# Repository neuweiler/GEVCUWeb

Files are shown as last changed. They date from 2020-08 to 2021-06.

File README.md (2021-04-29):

GEVCU - Web
=================
by Michael Neuweiler

A replacement for the buggy GEVCU iChip. Use an ESP32 to connect via the existing serial interface
of the GEVCU. It provides the GEVCU web-site and data via websocket to a web browser.

## Advantages
* The operation is much more stable
* The communication is much faster because it's binary between GEVCU and ESP32. Thus the json data
for the web-browser is generated by the ESP32, not GEVCU - off-loading GEVCU from time consuming work and reducing strings of 10-20 bytes to 2-3 bytes
* With SPIFFS' 1.5MB there's three times more space for web-content than on iChip. With an SD card we're talking GB's and the possibility to store and present statistical data.

The configuration of the ESP32 is stored in data/config.json. Adjust it to your own needs. 

Connect with a laptop, mobile phone, tablet or Raspberry Pi to the WiFi network of the ESP32 ("GEVCU" by default) and in a web-browser open http://gevcu.local 

## Required libraries
* ArduinoJson
* ArduinoOTA
* https://github.com/me-no-dev/AsyncTCP
* https://github.com/me-no-dev/ESPAsyncWebServer
* ESPmDNS
* FS
* SD_MMC
* SPIFFS
* Update
* WiFi
* HTTPClient
* WifiClientSecure

## Required hardware
* ESP32 board with GPIO 12-17 exposed - if possible with SD card reader integrated (then only 16,17 are required) - a good choice is https://www.aliexpress.com/item/4000133143167.html - although an SC card is not mandatory for operation, future extensions like storing statistical data
will require it.
* SD card with FAT file system to store the web site data on (you may also use 1.5MB SPIFFS instead).
Upload the contents of the directory "data" to the root of the file system.
* GEVCU (General Electric Vehicle Control Unit) to connect to via Serial2 interface.

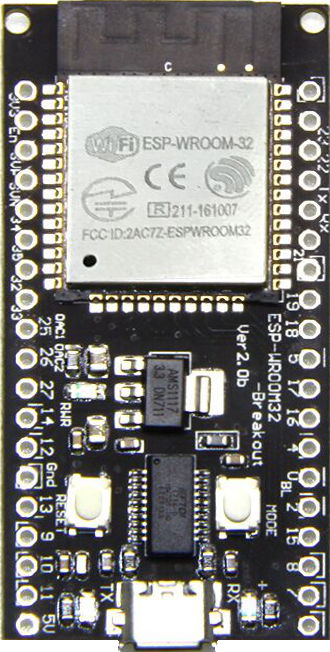
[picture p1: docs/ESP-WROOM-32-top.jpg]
BoardTop
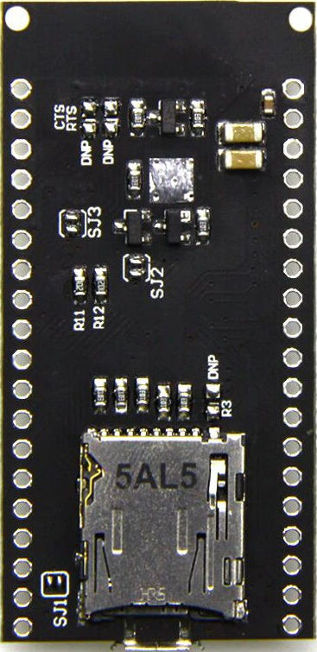
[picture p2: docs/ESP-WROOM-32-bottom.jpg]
BoardBottom
 

Note: To ensure flawless operation, increase the "max_files" config in SD_MMC.cpp from 5 to 20 !
      (in SDMMCFS::begin() , around line 72)

## Upload Parameters
* Board: ESP32 Dev Module
* Upload Speed: 921600
* CPU Freq: 240MHz
* Flash Freq: 80MHz
* Flash Mode: QIO
* Flash Size: 4MB (32Mb)
* Partition Scheme: Default with SPIFFS (1.2MB App, 1.5MB SPIFFS)
* Core Debug Level: none
* PSRAM: disabled
* Port: gevcu at 192.168.3.1 (for over the air update once a working copy has been installed via USB)

## Connect to GEVCU

The ESP32 must be connected the following way to GEVCU's wifi/iChip socket:
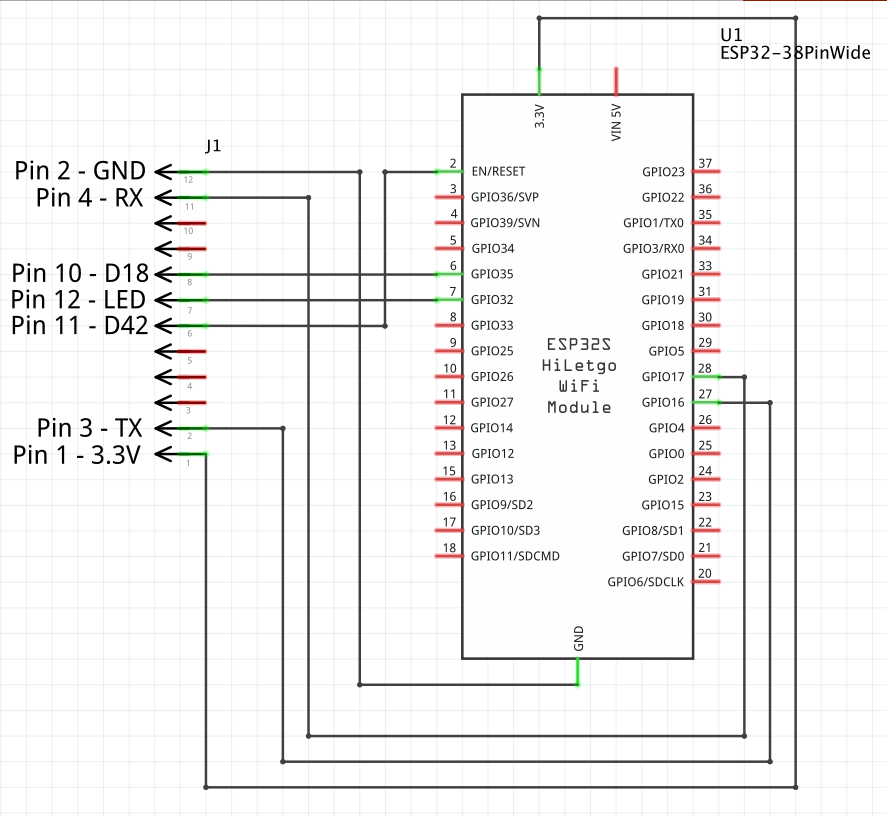
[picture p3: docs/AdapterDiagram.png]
Schema


With a simple adapter you can plug the ESP32 board right into the original socket. When creating the adapter board, make sure everything will fit in the GEVCU casing. And while you're at it, modify the board and attach an external antenna (like described here [External Antenna](https://www.hackster.io/simon-vavpotic/esp32-and-esp8266-external-antenna-f28e6b))
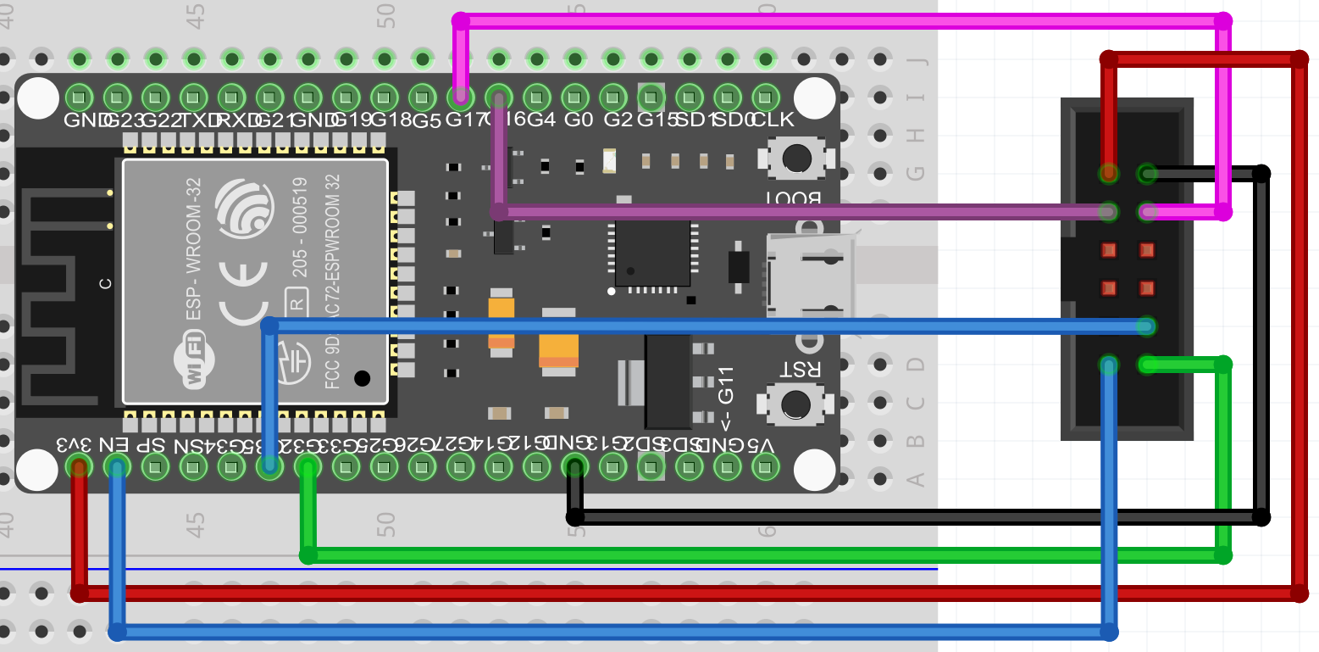
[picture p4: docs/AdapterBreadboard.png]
Adapter


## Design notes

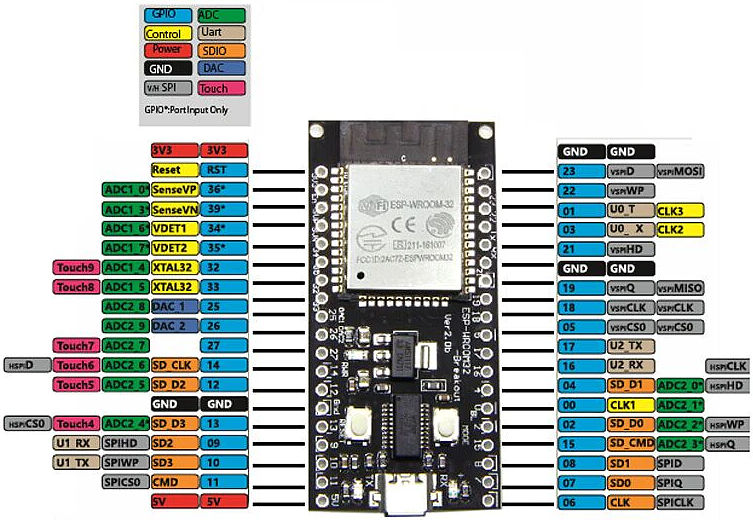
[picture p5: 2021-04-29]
docs/ESP-WROOM-32-pins.jpg

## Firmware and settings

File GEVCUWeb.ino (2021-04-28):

/*
 * GEVCU-ESP32Web.ino
 *
 Copyright (c) 2020 Michael Neuweiler

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
 */

#include "GEVCUWeb.h"

void setup() {
	logger.info("setup");

	config.load();

	wlan.init();
	webServer.init();
	webSocket.init(webServer.getWebServer());

	gevcuAdapter.init();

	heartBeat.init();
}

void loop() {
	delay(100);

	wlan.loop();
	gevcuAdapter.loop();
	webSocket.loop();
	heartBeat.loop();
}

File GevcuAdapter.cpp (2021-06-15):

/*
 * GevcuAdapter.cpp
 *
 Copyright (c) 2020 Michael Neuweiler

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
 */

#include "GevcuAdapter.h"

GevcuAdapter gevcuAdapter;

GevcuAdapter::GevcuAdapter() {
	bufPos = 0;
	binaryDataCount = 0;
	connectedClients = 0;
	timestamp = millis();
}

GevcuAdapter::~GevcuAdapter() {
}

void GevcuAdapter::init() {
	webSocket.subscribe(this);

	Serial2.begin(115200);
	Serial2.setRxBufferSize(4096);

	pinMode(PIN_GEVCU_LED, OUTPUT);
//    pinMode(PIN_GEVCU_RESERVED, OUTPUT);

	logger.info("GevcuAdapter configured");
}

String GevcuAdapter::getConfigParameter(String key) {
	return gevcuConfig[key];
}

void GevcuAdapter::setConfigParameter(String key, String value) {
	if (key && value && !value.equals(gevcuConfig[key])) {
		gevcuConfig[key] = value;
		Serial2.printf("cfg:%s=%s\r\n", key.c_str(), value.c_str());
		delay(50); // don't overwhelm GEVCU
	}
}

String GevcuAdapter::getLog() {
	Serial2.println("cmd:getLog");
	String log;
	uint32_t start = millis();
	while (Serial2.available() || (log.indexOf("LOG END") == -1 && (start + 3000) > millis())) {
		int ch = Serial2.read();
		if (ch != -1) {
			log.concat((char) ch);
		}
	}
	return log;
}

void GevcuAdapter::loop() {
	while (Serial2.available()) {
		int ch = Serial2.read();
//Serial.printf("%c (%X)\n", ch, ch);
		if (binaryDataCount > 0) { // expecting binary data
			serialBuffer[bufPos++] = ch;
			if (serialBuffer[0] == 0xaa) {
				if (bufPos > 2 && processBinaryData(serialBuffer[1], bufPos - 2, &serialBuffer[2])) {
					bufPos = 0;
					if (--binaryDataCount == 0) {
						String data;
						serializeJson(doc, data);
						if (logger.isDebug()) {
							logger.info("sending to websocket: %s", data.c_str());
						}
						webSocket.send(data);
					}
				}
			} else { // expecting binary data but got no valid lead char (0xaa) -> drop this entry
				logger.warn("dropping invalid data frame");
				bufPos = 0;
				binaryDataCount--;
			}
		} else if (ch == 13 || ch == 10 || ch == 0 || bufPos > SERIAL_BUFFER_SIZE - 1) { // process config/log data
			serialBuffer[bufPos] = 0;
			if (bufPos > 4) { // drop strings smaller than 4 characters
				processInput(serialBuffer);
			}
			bufPos = 0;
		} else if (ch != -1) {
			serialBuffer[bufPos++] = ch;
		}
	}

	if (timestamp + 10000 < millis()) {
		// if config is not loaded, request from GEVCU
		if (gevcuConfig["logLevel"] == NULL) {
			logger.warn("GEVCU config not loaded, requesting");
			Serial2.println("cmd:loadConfig");
		}
		String timeRunning = "{\"timeRunning\": \"" + getTimeRunning() + "\"}";
		webSocket.send(timeRunning);

		timestamp = millis();
	}
}

bool GevcuAdapter::processBinaryData(char code, uint16_t len, char *data) {
	DataPoint *dp = findDataPoint(code);
	if (dp && len < dp->length) {
		return false;
	}

	if (dp->length == 1 && dp->unsignd) {
		doc[dp->label] = (uint8_t) data[0];
	} else if (dp->length == 2 && dp->unsignd) {
		doc[dp->label] = (dp->divisor == 0 ? readUInt16(data) : readUInt16(data) / (double) dp->divisor);
	} else if (dp->length == 2 && !dp->unsignd) {
		doc[dp->label] = (dp->divisor == 0 ? readInt16(data) : readInt16(data) / (double) dp->divisor);
	} else if (dp->length == 4 && dp->unsignd) {
		doc[dp->label] = serialized(
				(dp->divisor == 0 ? String(readUInt32(data)) : String(readUInt32(data) / (double) dp->divisor)));
	} else {
		logger.warn("unable to process data: code %d, length %d", code, len);
	}
	return true;
}

uint32_t GevcuAdapter::readUInt32(char *data) {
	return (uint32_t) ((data[0] << 24) | (data[1] << 16) | (data[2] << 8) | data[3]);
}

int16_t GevcuAdapter::readInt16(char *data) {
	return (int16_t) ((data[0] << 8) | data[1]);
}

uint16_t GevcuAdapter::readUInt16(char *data) {
	return (uint16_t) ((data[0] << 8) | data[1]);
}

void GevcuAdapter::processInput(String input) {
	if (logger.isDebug()) {
		logger.debug("input from GEVCU: %s", input.c_str());
	}

	String data = extractData(input, "data:");
	if (data.length()) {
		binaryDataCount = data.toInt();
		doc.clear();
		return;
	}

	data = extractData(input, "cfg:");
	if (data.length()) {
		int pos = data.indexOf('=');
		if (pos > 0) {
			String key = data.substring(0, pos);
			String value = data.substring(pos + 1);
			gevcuConfig[key] = value;
		}
		return;
	}

	data = extractData(input, "json:");
	if (data.length()) {
		webSocket.send(data);
		return;
	}
	logger.warn("unknown data from GEVCU: %s", input.c_str());
}

String GevcuAdapter::extractData(String input, String identifier) {
	int index = input.indexOf(identifier);
	if (index == -1)
		return "";
	return input.substring(index + identifier.length());
}

void GevcuAdapter::event(String message) {
	if (message.equals("disconnected")) {
		if (--connectedClients == 0) {
			digitalWrite(PIN_GEVCU_LED, LOW);
			Serial2.printf("cmd:%s\r\n", message.c_str());
		}
	} else {
		if (message.equals("connected")) {
			connectedClients++;
			digitalWrite(PIN_GEVCU_LED, HIGH);
		}
		Serial2.printf("cmd:%s\r\n", message.c_str());
	}
}

void GevcuAdapter::sendHeartBeat(uint16_t count) {
	Serial2.printf("hb:%d\r\n", count);
}

void GevcuAdapter::stopHeartBeat() {
	Serial2.println("hb:stop");
}

void GevcuAdapter::startHeartBeat() {
	Serial2.println("hb:start");
}

DataPoint* GevcuAdapter::findDataPoint(char code) {
	for (int i = 0; i < sizeof(dataPoints); i++) {
		if (dataPoints[i].code == code) {
			return &dataPoints[i];
		}
	}
	return NULL;
}

/**
 * \brief Calculate the runtime in hh:mm:ss
 *
 * \return the current time running in hh:mm:ss
 */
String GevcuAdapter::getTimeRunning() {
	char buffer[10];
	uint32_t ms = millis();
	int seconds = (int) (ms / 1000) % 60;
	int minutes = (int) ((ms / (1000 * 60)) % 60);
	int hours = (int) ((ms / (1000 * 3600)) % 24);
	sprintf(buffer, "%02d:%02d:%02d", hours, minutes, seconds);
	return String(buffer);
}

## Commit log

2020-02-22 refactor and split to classes first working test with files on SD card
    [Configuration.h]
2020-03-07 use ArduinoJson
2020-03-07 responsive grid layout throttleSettings larger/nicer color
2020-03-14 fix devices tab, refactor config table
2020-03-31 clean-up, add copyright notice
    [Configuration.h]
2020-04-13 first running spike between ESP32 and GEVCU
2020-04-13 prevent errors when socket is already down
2020-04-13 also transmit unchecked checkboxes add missing values minor fixes
    [GevcuAdapter.cpp]
2020-04-13 correctly pre-load Led font for gauges
2020-04-13 auto re-load config params (e.g. after crash)
    [GevcuAdapter.cpp]
2020-04-20 Added diagram for GEVCU/ESP32 adapter
    [GEVCU-ESP32-Adapter.fzz]
2020-05-23 try to get system state again in case it never arrives
2020-05-23 add support for torqueAvailable in gauges
2020-08-03 send heart-beat rewire so GEVCU can reset via EN pin
    [GEVCU-ESP32-Adapter.fzz]
2020-08-05 add retrieval of log history add heartbeating so GEVCU can determine whether to reset ESP or not
    [GevcuAdapter.cpp]
2020-08-07 make led stay on when websocket is connected
2020-08-07 Support values for voltage drop in input current
2020-10-22 update arduino plugin
2020-10-24 correct data types for remaining charge time
2021-04-28 make config items camel case
    [Configuration.h]
2021-04-28 move wifi and OTA handling to WLAN class WLAN pulls info about max available current from remote host
2021-04-28 reformat only, long live tabs ! :)
    [Configuration.h]
2021-04-28 retrieve maxCurrent parametrize wifi adresses
    [Configuration.h]
2021-04-28 move config to a file add flexible filehandler which copes with SD_MMC and SPIFFS
    [Configuration.h]
2021-04-29 extend documentation, incl. pictures of correct board
2021-04-30 restructure config, add ap hostname,ip,gw,mask,channel
    [Configuration.h]
2021-08-07 improve adjusting charge input level
